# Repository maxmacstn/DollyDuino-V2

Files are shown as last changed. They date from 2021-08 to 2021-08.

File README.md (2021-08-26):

# DollyDuino 2.0
ESP32 Based camera motion controller, implement based on Arduino and PlatformIO. This project is the successor from my [orginal design](https://github.com/maxmacstn/Arduino-Motorized-Dolly).

**Video:**  https://youtu.be/K7UvhgVBU1E

⚠️ This project is currently in the development process, it might contain some unfinished features or bugs. However, it was functioning quite well so far.

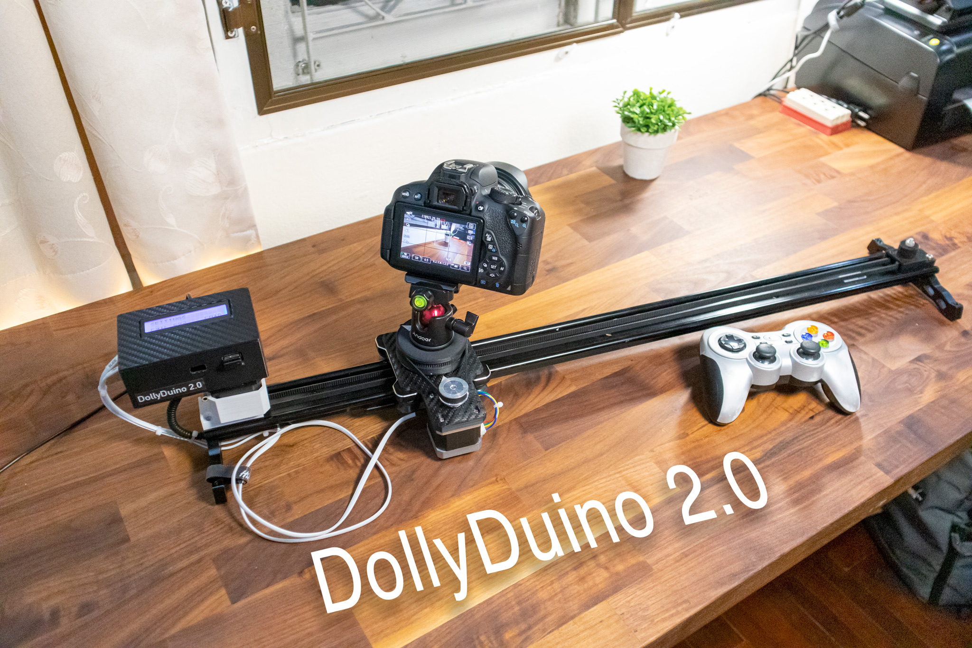
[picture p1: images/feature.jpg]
Bluetooth Remote for Modern Canon Cameras


## Features

* 2 Axis control: Slide & Pan.
* 16x2 LCD Display.
* Controlled by USB HID interface gamepad.
* Built-in Canon EOS Camera remote using Bluetooth LE.
* USB-C PD Power input.
* USB-A power out for powering the camera or charging.

## Modes

1. Manual/Slide - Operate the camera movement manually using a gamepad, or set the automatic linear movement with smooth acceleration/deceleration.
2. Orbit Mode - Lock the camera facing towards the object while sliding.
3. Time lapse - Precise micro-movement with automatic camera triggering system.

## Major components
Please see full list of components and parts in [Bill of Materials](https://github.com/maxmacstn/DollyDuino-V2/blob/main/BOM.xlsx).
- Andeor camera slider.
- DollyDuino 2.0 controller.
	- Node32 Lite development board.
	- TMC2226 silent stepper driver.
	- LCD 16x2 Display.
	- ZY12PDN USB-C PD Module.
	- Mini USB Host shield.
- NEMA 17 Stepper Driver
- GT2 Timing belt and pulley wheels.
- A bunch of 3D-Printed parts.

## Gamepad buttons

| Button | Function |
|---|---|
| A | Trigger camera shutter |
| B | Clear in/out point, Stop auto slide |
| X | Unlock motors |
| Y | Set in/out point |
| Left | Previous mode |
| Right  | Next Mode |
| Up | Increment Interval |
| Down | Decrement Interval |
| LT | Decrement shutter speed |
| RT | Increment shutter speed |
| LB | Decrease sliding speed |
| RB | Increase sliding speed |
| Start  | Start auto sliding movement |
| Back | Override all axis position as home position (0) |

## References 
-  [3D Printed Motorised DSLR Camera Slider by issac879](https://www.youtube.com/watch?v=v1b7Wvu87-U)
- [Mini USB Host shield with esp8266](https://create.arduino.cc/projecthub/139994/plug-any-usb-device-on-an-esp8266-e0ca8a)

## To-do
- [ ] Fix bug in timelapse mode, the slider should not move when the camera shutter is opening.
- [ ] Re-design pan axis to be more rigid.
- [ ] Improve usability.

Feel free to contribute!

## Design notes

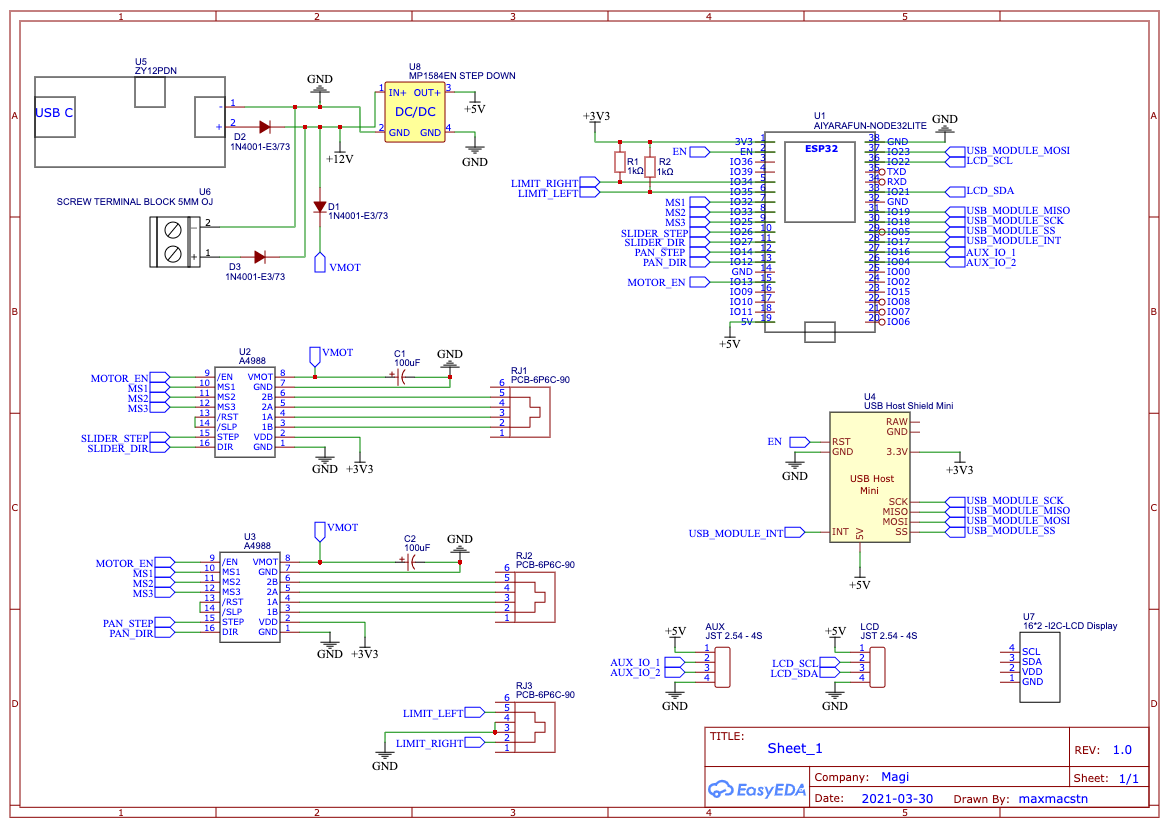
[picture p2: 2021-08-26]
PCB/Schematic_DollyDuino2_2021-08-26.png

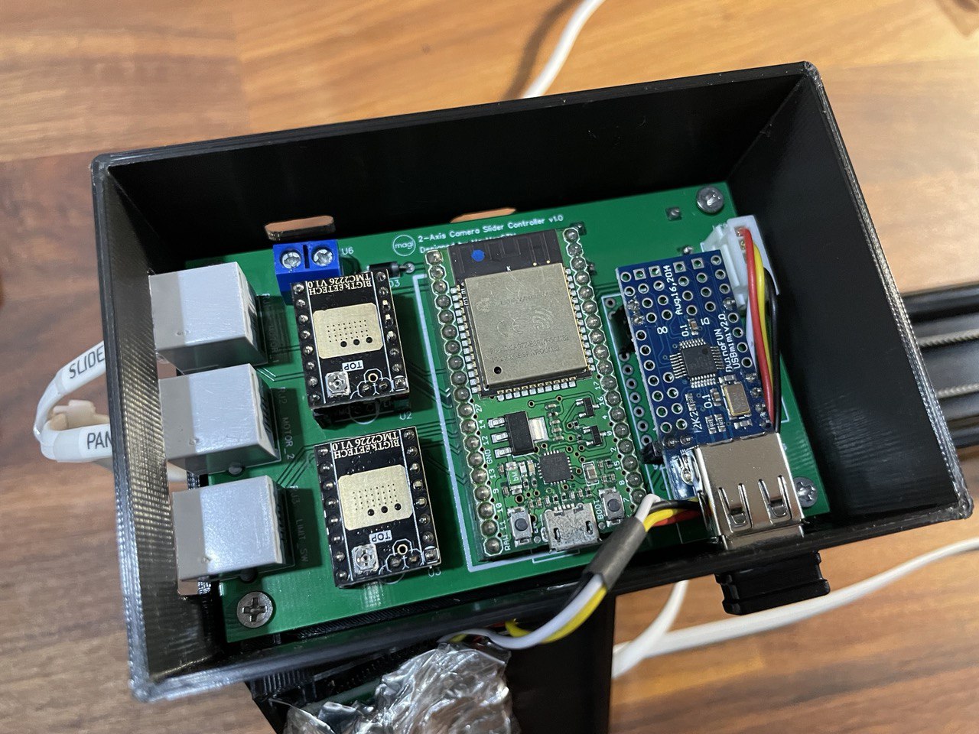
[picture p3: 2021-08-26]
images/controller_inside.jpeg

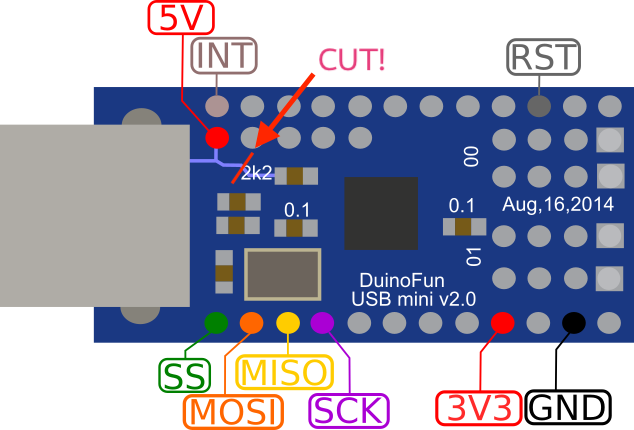
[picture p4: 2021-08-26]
References/usbhost_mini_3v_convert.png

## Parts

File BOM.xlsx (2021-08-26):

DollyDuino2.0 Bill of materials |  |  |  | By MaxMacSTN
Part | Name | Links | Qty
Base | Andoer Slider 80 CM | https://www.lazada.co.th/products/andoer-80-5-ca-nonni-konso-nydslrdv-i302700572-s521866836.html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 | 1
 | Andoer Ball Head small | https://www.lazada.co.th/products/andoer-canon-nikon-sony-dslr-mirrorless-i300828203-s518186201.html?mp=1 | 1
Rail ASSY | GT2 timing belt width 6mm (2 Metres) | https://www.zonemaker.com/product/36/2gt-6mm-rubber-open-timing-belt-%E0%B8%A3%E0%B8%B2%E0%B8%84%E0%B8%B2-1%E0%B9%80%E0%B8%A1%E0%B8%95%E0%B8%A3-2 | 1
 | 2GT Width 6mm, 20 Teeth Timing Pulley (Bore 5mm) | https://www.zonemaker.com/product/65/2gt-width-6mm-20-teeth-timing-pulley-bore-5mm | 1
 | Pulley Wheel 20 Teeth 2GT | https://www.zonemaker.com/product/609/pulley-wheel-20-%E0%B8%9F%E0%B8%B1%E0%B8%99-2gt-width-6mm-belt-bore-5mm | 1
 | Belt closed loop rubber 280-2GT-6 (Closed-loop length 280mm, GT2 timing belt, width 6mm) | https://www.zonemaker.com/product/609/pulley-wheel-20-%E0%B8%9F%E0%B8%B1%E0%B8%99-2gt-width-6mm-belt-bore-5mm | 1
 | [3D Print] slide motor mount |  | 1
 | [3D Print] slide pully wheel mount |  | 1
 | M4 Nuts & Bolts for securing pulley wheel |  | 1
Sliding plate ASSY | 2GT Width 6mm, 36 Teeth Timing Pulley Bore (Bore 5mm) | https://www.zonemaker.com/product/2366/2gt-width-6mm-36-teeth-timing-pulley-bore-bore-5mm | 1
 | GT2 Belt closed loop rubber 280-2GT-6 (Closed-loop length 280mm, GT2 timing belt, width 6mm) | https://www.zonemaker.com/product/1621/belt-closed-loop-rubber-280-2gt-6-closed-loop-length-280mm-gt2-timing-belt-width-6mm-2 | 1
 | Timing Belt Fixing Clamp 9*40mm | https://www.zonemaker.com/product/402/timing-belt-fixing-clamp-9x40mm-tooth-pitch-2mm-aluminum-alloy | 1
 | [3D Print] Timing Belt Clamp mount |  | 1
 | [3D Print] Ball Head Mount Top |  | 1
 | [3D Print] Ball Head Mount Bottom |  | 1
 | [3D Print] Inner Bearing Holder |  | 1
 | [3D Print] Inner Bearing Washer |  | 1
 | [3D Print] Sliding Plate Mount |  | 1
 | [3D Print] Sliding Plate Mount Clamp |  | 1
 | M2x4 Countersunk Screw |  | 1
 | M3x8 Countersunk Screw |  | 1
 | M3x10 Countersunk Screw |  | 1
 | M3x8 Screw |  | 1
 | M6 Bolt |  | 1
 | M3 Nut and Bolt (for belt clamp) |  | 1
 | Deep Grove Bering 6808ZZ (bore:40mm OD:52mm Width:7mm) | https://shopee.co.th/6806ZZ-~-6810ZZ-%E0%B8%95%E0%B8%A5%E0%B8%B1%E0%B8%9A%E0%B8%A5%E0%B8%B9%E0%B8%81%E0%B8%9B%E0%B8%B7%E0%B8%99%E0%B9%80%E0%B8%A1%E0%B9%87%E0%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 | 1
Controller | ESP32 AIYARAFUN-Node32 Lite |  | 1
 | DollyDuino2.0 PCB |  | 1
 | Capacitor 100uF |  | 2
 | Diode 1N4001 |  | 4
 | Resistor 1KΩ 5W |  | 2
 | USB Host Shield Mini |  | 1
 | ZY12PDN USB-C PD Module |  | 1
 | MP1584EN STEP DOWN module 5V |  | 1
 | BIQU TMC2226 V1.0 Stepper Driver | https://shopee.co.th/BIQU-TMC2226-V1.0-Driver-for-3D-Printer-i.43378426.4744022662 | 2
 | JST Header JST 2.54 - 4S |  | 2
 | SCREW TERMINAL BLOCK 5MM |  | 1
 | RJ11 6P6C Female PCB Mount |  | 3
 | LCD 16x2 I2C |  | 1
 | [3D Print] controller_lid |  | 1
 | [3D Print] controller_enclosure_body |  | 1
 | [3D Print] controller_enclosure_lid |  | 1
Motors and wires | Nema 17 Stepper Driver |  | 2
 | Telephone Wire RJ11 4P |  | 1
Gamepad | Logitech F710 |  | 1

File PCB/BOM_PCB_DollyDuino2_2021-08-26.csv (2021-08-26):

ID | Name | Designator | Footprint | Quantity | Manufacturer Part | Manufacturer | Supplier | Supplier Part | Price | Pins | 3DModel | LCSC Assembly | Paste Type | Contributor | SMT Type | link
1 | MP1584EN STEP DOWN | U8 | MP1584EN | 1 |  |  |  |  |  | 4 |  |  |  | zdravko.kreze
2 | 1N4001-E3/73 | D3,D1,D2 | DO-41_BD2.4-L4.7-P8.70-D0.9-RD | 3 | 1N4001-E3/73 | VISHAY | LCSC | C145491 | 0.155 | 2 | DO-41_D2.8-L4.2-P8.00 | Yes | expand | LCSC | Extend | https://item.szlcsc.com/85412.html
3 | A4988 | U2,U3 | A4988 | 2 | A4988 |  |  |  |  | 16 |  |  |  | rom1nux |  | https://www.pololu.com/file/0J450/a4988_DMOS_microstepping_driver_with_translator.pdf
4 | USB Host Shield Mini | U4 | ARDUINO USB HOST SHIELD MINI - BRETT | 1 |  |  |  |  |  | 25 |  |  |  | SparkFun
5 | AIYARAFUN-NODE32LITE | U1 | NODE32S-PCBLIB | 1 | New SchematicLib |  |  |  |  | 38 |  |  |  | marcos.miasiro
6 | 100uF | C1,C2 | CAP-TH_BD5.0-P2.00-D0.8-FD | 2 | 100uF 25V 5*11 | ValuePro | LCSC | C47873 | 0.012 | 2 | CAP-TH_D5.0×H7.0×P2.0 | Yes | expand | 官方封装库 | Extend | https://item.szlcsc.com/44805.html
7 | PCB-6P6C-90 | RJ1,RJ2,RJ3 | RJ11-TH_PCB-6P6C-90 | 3 | - | Shenzhen Cankemeng | LCSC | C189750 | 0.16 | 6 | RJ11-TH_PCB-6P6C-90 | Yes | expand | LCSC | Extend | https://item.szlcsc.com/203237.html
8 | 1kΩ | R1,R2 | RES-TH_BD2.5-L6.5-P10.50-D0.6 | 2 | CF1/4W-1.8KΩ±5%T52 | Huaxing Mechanical-Elec. | LCSC | C714304 | 0.005 | 2 | RES-TH_D2.3-L6.5-P10.50 |  |  | LCSC |  | https://item.szlcsc.com/204066.html
9 | SCREW TERMINAL BLOCK 5MM OJ | U6 | SCREW TERMINAL BLOCK 5MM | 1 | Screw Terminal Block 5mm |  |  |  |  | 2 |  |  |  | luizwenner
10 | JST 2.54 - 4S | AUX,LCD | CONECTOR JST 2.54 - 4S | 2 |  |  |  |  |  | 4 |  |  |  | aristijuango
11 | ZY12PDN | U5 | ZY12PDN | 1 |  |  |  |  |  | 2 |  |  |  | superpolynomialtime

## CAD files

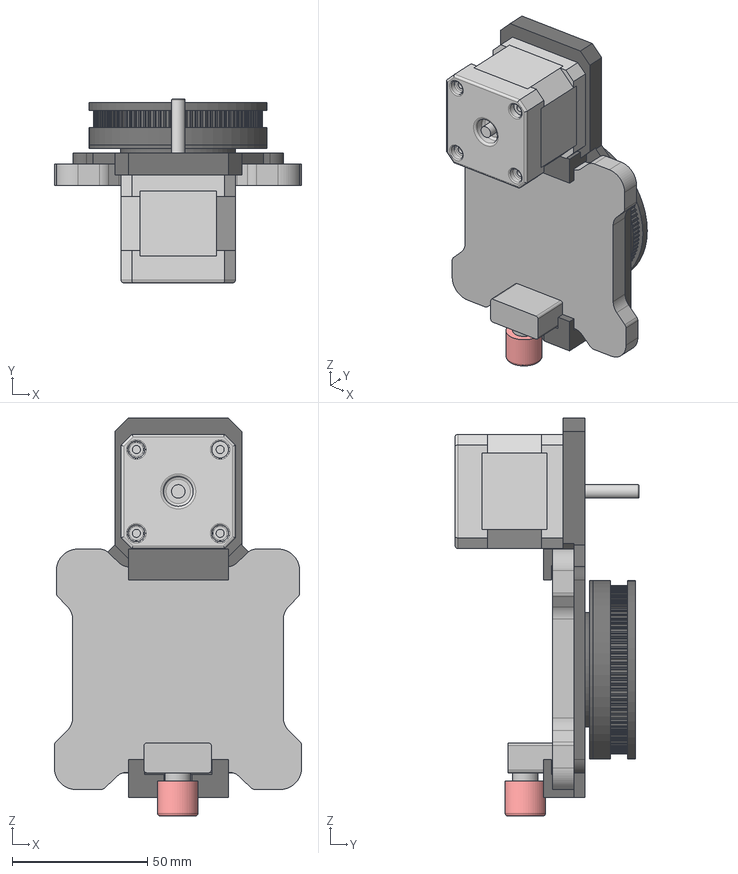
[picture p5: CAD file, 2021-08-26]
3D/STEP/sliding_plate_assy.step
91.5 x 68.0 x 147.3 mm
inner_bearing_holder
inner bearing holder washer
Base
Cuerpo
Tapa
Eje
GT2 Timing Pulley generator v4

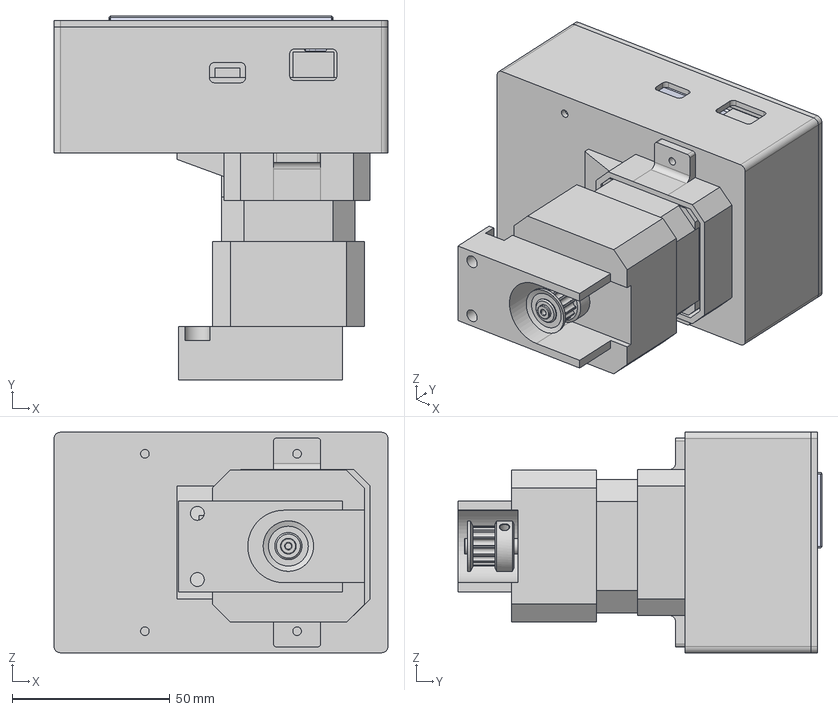
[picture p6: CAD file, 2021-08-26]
3D/STEP/controller_enclosure_assy.step
106.0 x 115.4 x 70.0 mm
PCB
LCD_1
Base
Cuerpo
Tapa
Eje
T5 Pulley

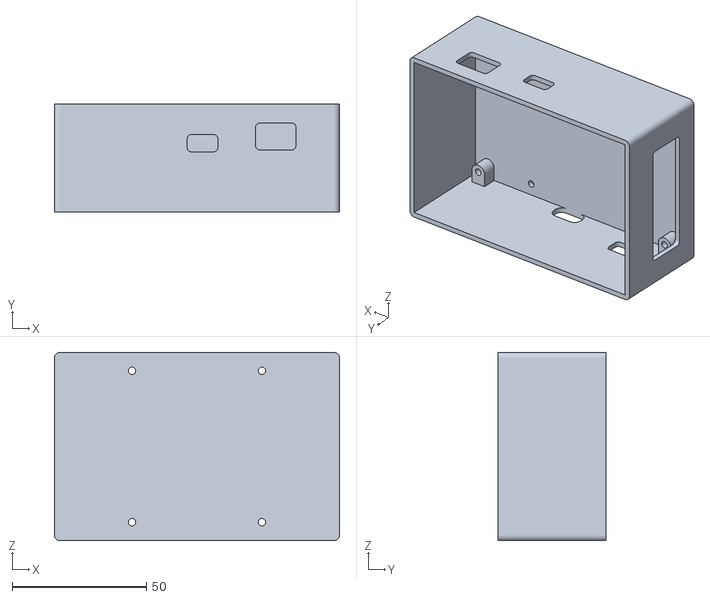
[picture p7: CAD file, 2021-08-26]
3D/STL/controller_enclosure_body.stl
106.0 x 40.0 x 70.0

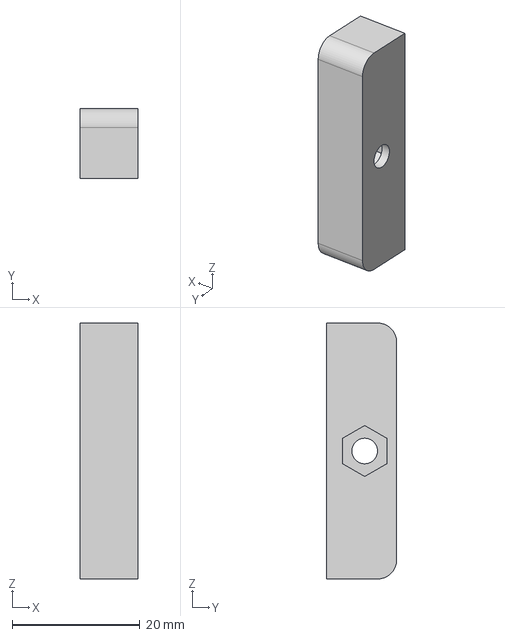
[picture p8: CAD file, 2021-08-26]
3D/STEP/timing_belt_clamp_mount.step
9.00 x 11.0 x 40.0 mm

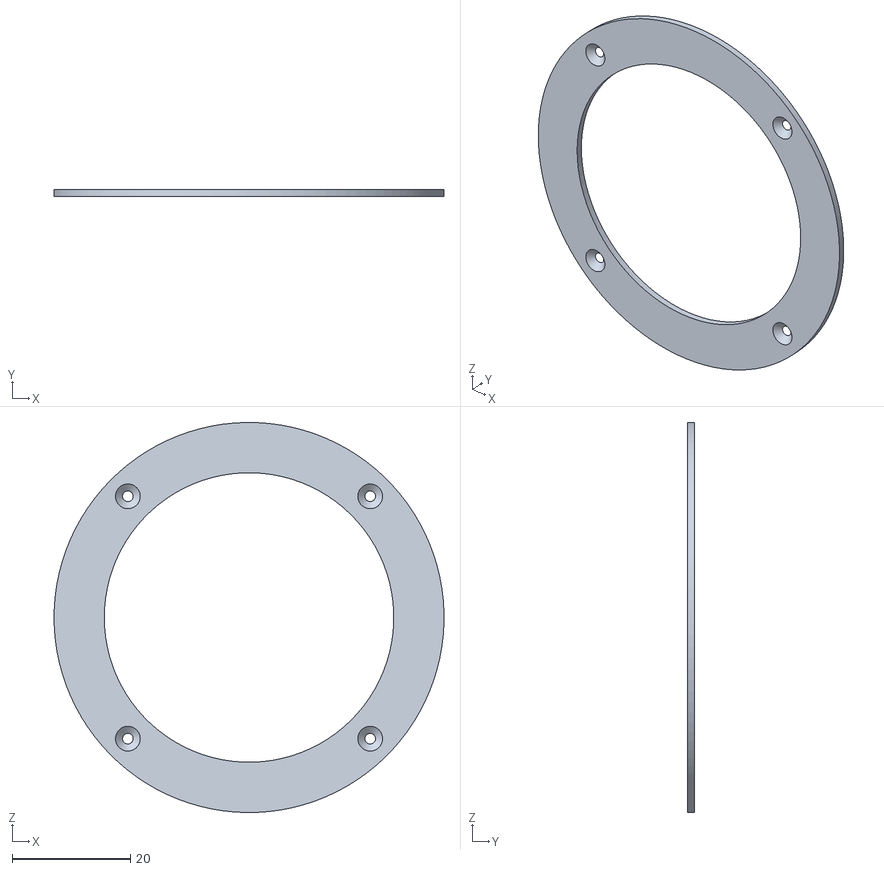
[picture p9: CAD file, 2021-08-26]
3D/STL/ball_head_mount_bottom.stl
66.0 x 1.20 x 66.0

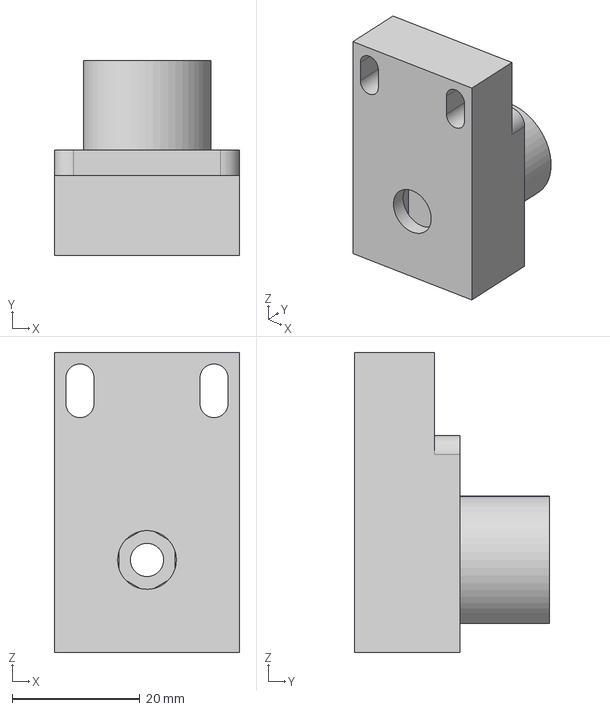
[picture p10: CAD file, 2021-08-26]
3D/STEP/slide_pully_wheel_mount.step
29.0 x 30.5 x 47.0 mm

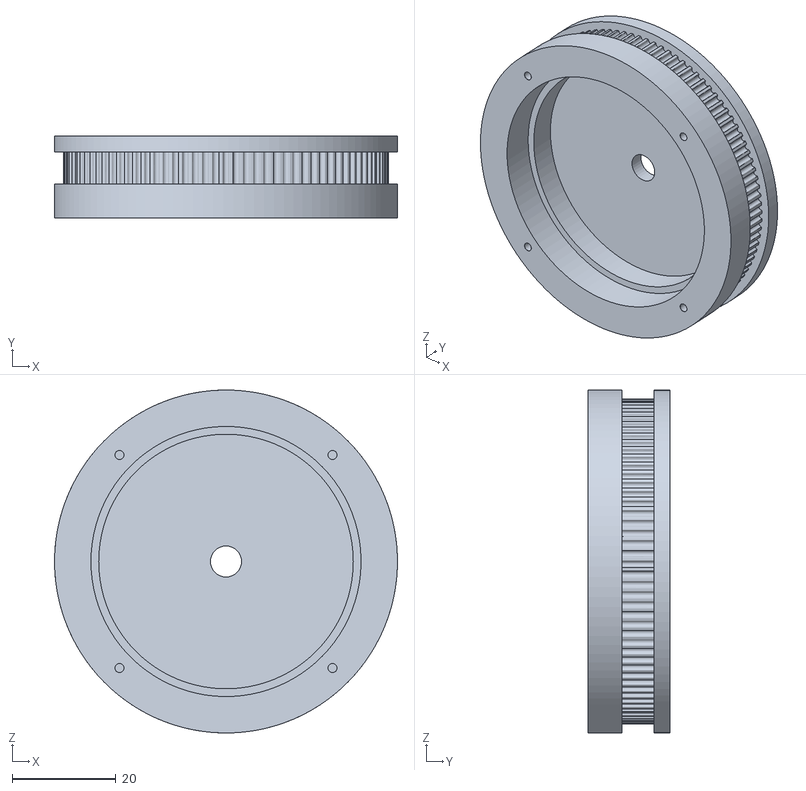
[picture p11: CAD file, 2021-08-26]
3D/STL/ball_head_mount_top.stl
66.0 x 15.7 x 66.0

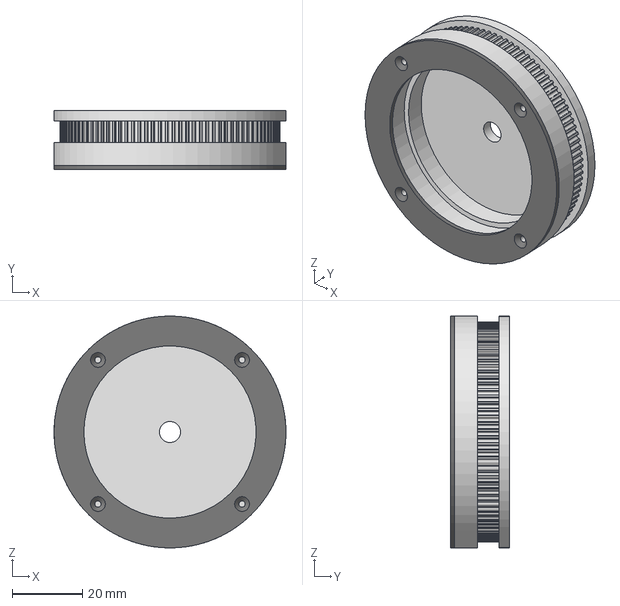
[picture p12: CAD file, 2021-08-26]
3D/STEP/ball_head_mount.step
66.0 x 16.9 x 66.0 mm

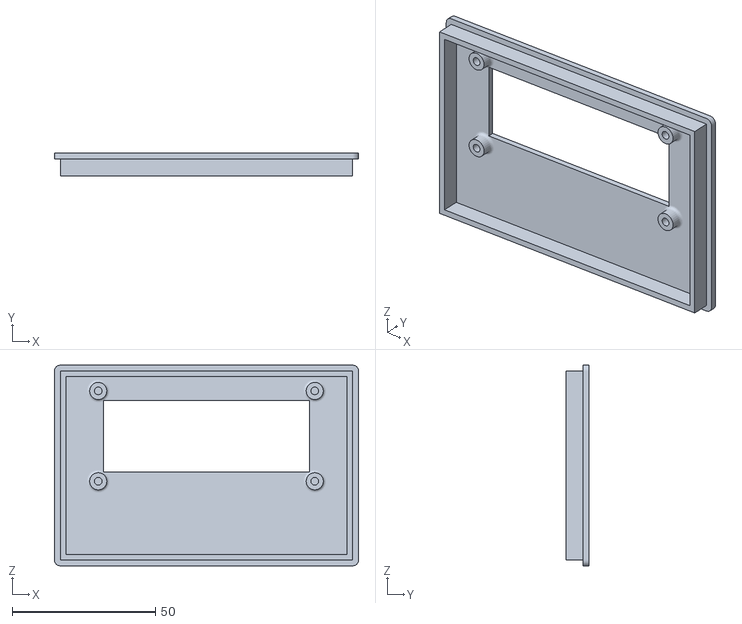
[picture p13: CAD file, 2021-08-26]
3D/STL/controller_lid.stl
106.0 x 8.00 x 70.0

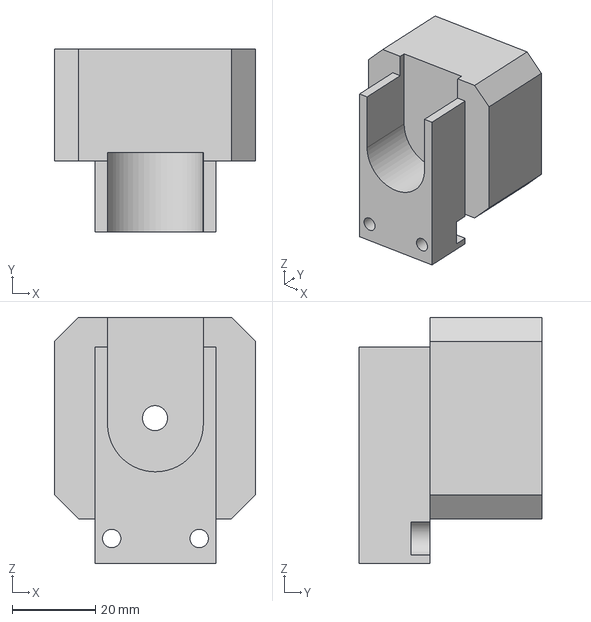
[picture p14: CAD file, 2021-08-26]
3D/STEP/slider_motor_mount.step
48.3 x 43.9 x 59.0 mm

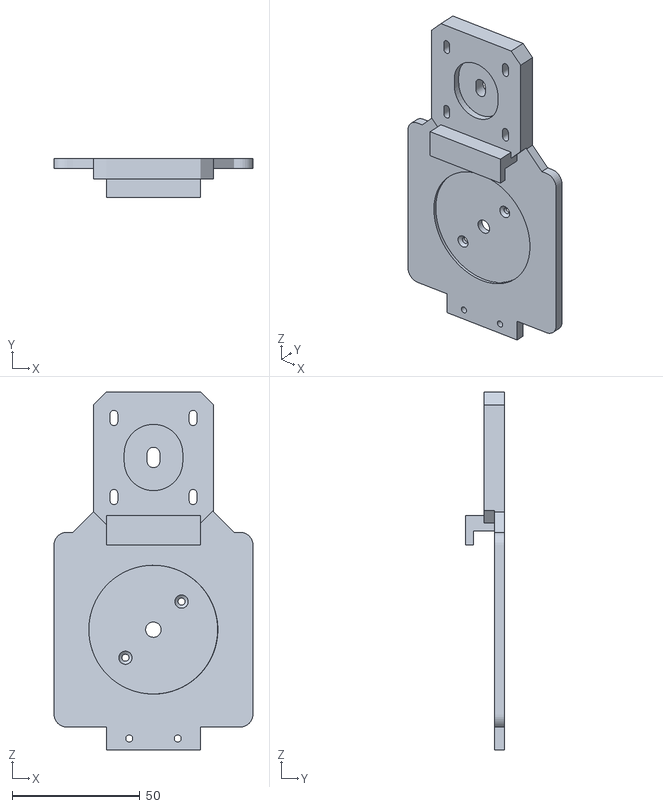
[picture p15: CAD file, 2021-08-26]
3D/STL/sliding_plate_mount.stl
78.0 x 15.3 x 140.3

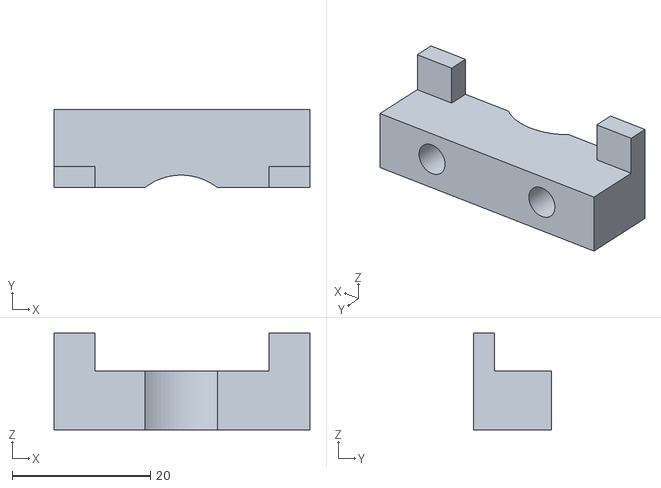
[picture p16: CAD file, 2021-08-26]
3D/STL/sliding_plate_mount_clamp.stl
37.0 x 11.3 x 14.0

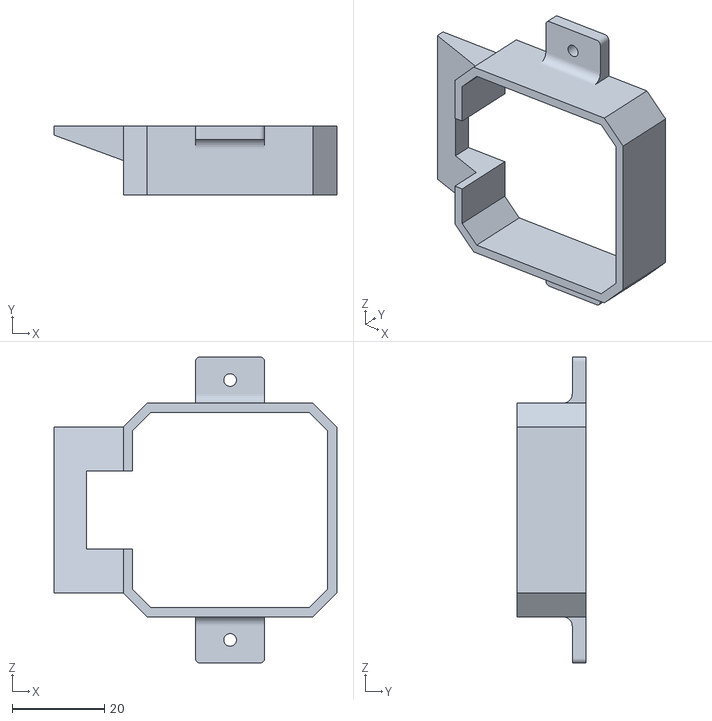
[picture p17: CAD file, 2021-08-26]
3D/STL/controller_enclosure_motor_mount.stl
61.3 x 15.0 x 66.3

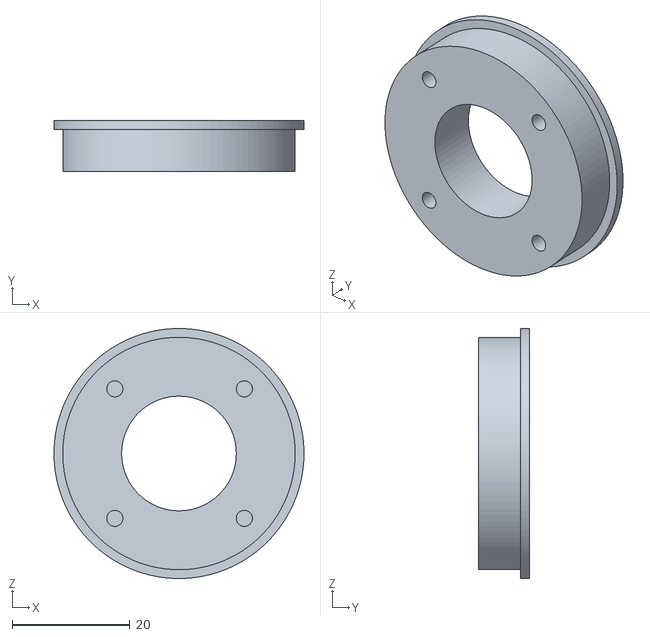
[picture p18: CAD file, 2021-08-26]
3D/STL/inner_bearing_holder.stl
42.5 x 8.60 x 42.5

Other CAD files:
3D/STL/inner_bearing_holder_washer.stl
3D/STL/slide_pully_wheel_mount.stl
3D/STL/slider_motor_mount.stl
3D/STL/timing_belt_clamp_mount.stl

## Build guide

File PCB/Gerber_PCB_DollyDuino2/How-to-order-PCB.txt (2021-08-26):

How to Order PCB

Please refer to:
https://docs.easyeda.com/en/PCB/Order-PCB

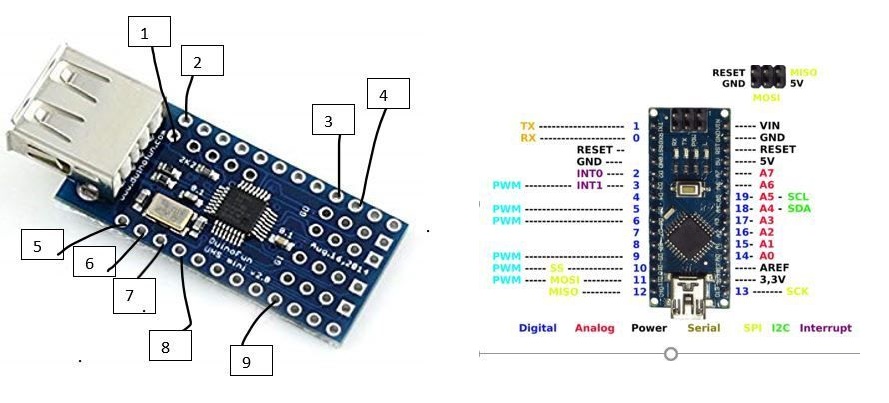
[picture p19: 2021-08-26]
References/arduino_nano_usb_host_shield_wiring_PWkan4VJHw.jpg

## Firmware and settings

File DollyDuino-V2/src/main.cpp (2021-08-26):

#include <Arduino.h>
#include <usbhid.h>
#include <hiduniversal.h>
#include <usbhub.h>
#include "hidjoystickrptparser.h"
#include "Slider.h"
#include "AccelStepper.h"

USB Usb;
USBHub Hub(&Usb);
HIDUniversal Hid(&Usb); //Default pins use P5, P17 for ESP32 board for SPI_SS and INTR
JoystickEvents JoyEvents;
JoystickReportParser Joy(&JoyEvents);
TaskHandle_t usbTaskHandle;

byte gamePadRpos = 127;

Slider slider = Slider();

#define GAMEPAD_BUTTON_A 2
#define GAMEPAD_BUTTON_B 3
#define GAMEPAD_BUTTON_X 1
#define GAMEPAD_BUTTON_Y 4
#define GAMEPAD_BUTTON_UP 00
#define GAMEPAD_BUTTON_DN 04
#define GAMEPAD_BUTTON_L 06
#define GAMEPAD_BUTTON_R 02
#define GAMEPAD_BUTTON_LB 5
#define GAMEPAD_BUTTON_RB 6
#define GAMEPAD_BUTTON_LT 7
#define GAMEPAD_BUTTON_RT 8
#define GAMEPAD_BUTTON_BACK 9
#define GAMEPAD_BUTTON_START 10

void usbTask( void * pvParameters ){
  for(;;){
        Usb.Task();
        vTaskDelay(1);
  }
}



void setup()
{
        // Serial.begin(115200);
        Serial.println("Start");
        slider.init();
        if (Usb.Init() == -1){
                Serial.println("OSC did not start.");
                slider.displayBootMessage("USB Error");
                while(1){};
        }
        delay(200);
        if (!Hid.SetReportParser(0, &Joy)){
                ErrorMessage<uint8_t>(PSTR("SetReportParser"), 1);
                slider.displayBootMessage("USB Parser error");
                while(1){};
        }
        
        slider.displayBootMessage("USB OK!");
        for(int i = 0; i <100; i++){
                Usb.Task();
                delay(10);
        }

        slider.onAnalogStickChanged(0x80, 0x80,  0x80, 0x80);
        
        
}


void loop()
{
        // put your main code here, to run repeatedly:
        Usb.Task();
        slider.run();
        slider.updateScreen();

        // stepper_pan.run();
        // float currentPanSpeed = map(abs(gamePadRpos-128),0,128,0,panDegreesToSteps(180));
        // if (gamePadRpos > 129 ){
        //         stepper_pan.moveTo(stepper_pan.currentPosition() + 1);
        //         stepper_pan.setSpeed(currentPanSpeed);
        // }else if( gamePadRpos < 125 ){
        //         stepper_pan.moveTo(stepper_pan.currentPosition() - 1);
        //         stepper_pan.setSpeed(-currentPanSpeed);

        // }



}

void JoystickEvents::OnGamePadChanged(const GamePadEventData *evt)
{
        Serial.print("X1: ");
        PrintHex<uint8_t>(evt->X, 0x80);
        Serial.print("\tY1: ");
        PrintHex<uint8_t>(evt->Y, 0x80);
        Serial.print("\tX2: ");
        PrintHex<uint8_t>(evt->Z1, 0x80);
        Serial.print("\tY2: ");
        PrintHex<uint8_t>(evt->Z2, 0x80);
        Serial.print("\tRz: ");
        PrintHex<uint8_t>(evt->Rz, 0x80);
        Serial.println("");

        // analogLposX = evt->Y;
        // analogLposY = evt->Z1;
        // analogRposX = evt->Z2;
        // analogRposY = evt->Rz;


        slider.onAnalogStickChanged(evt->Y, evt->Z1,  evt->Z2, evt->Rz);
}

void JoystickEvents::OnHatSwitch(uint8_t hat)
{
        Serial.print("Hat Switch: ");
        PrintHex<uint8_t>(hat, 0x80);
        Serial.println("");

        switch (hat)
        {
        case GAMEPAD_BUTTON_L:
                slider.onPreviousModeButtonPressed();
                break;
        case GAMEPAD_BUTTON_R:
                slider.onNextModeButtonPressed();
                break;
        case GAMEPAD_BUTTON_UP:
                slider.onUpButtonPressed();
                break;
        case GAMEPAD_BUTTON_DN:
                slider.onDnButtonPressed();
                break;
        default:
                break;
        }
}

void JoystickEvents::OnButtonUp(uint8_t but_id)
{
        Serial.print("Up: ");
        Serial.println(but_id, DEC);
        switch (but_id)
        {
        case GAMEPAD_BUTTON_Y:
                slider.disableAllMotors(false);
        

        default:
                break;
        }
}

void JoystickEvents::OnButtonDn(uint8_t but_id)
{
        Serial.print("Dn: ");
        Serial.println(but_id, DEC);

        switch (but_id)
        {
        case GAMEPAD_BUTTON_A:
                slider.onActionButtonPressed();
                // Serial.println("Trigger");
                // canon_ble.triggerPhoto();
                break;
        case GAMEPAD_BUTTON_START:
                slider.onStartButtonPressed();
                break;
        case GAMEPAD_BUTTON_B:
                slider.onBackButtonPressed();
                break;
        case GAMEPAD_BUTTON_LB:
                slider.onLBButtonPressed();
                break;
        case GAMEPAD_BUTTON_RB:
                slider.onRBButtonPressed();
                break;
        case GAMEPAD_BUTTON_Y:
                slider.onAddKeyFrameButtonPressed();
                break;
        case GAMEPAD_BUTTON_LT:
                slider.onLTButtonPressed();
                break;
        case GAMEPAD_BUTTON_RT:
                slider.onRTButtonPressed();
                break;

        case GAMEPAD_BUTTON_X:
                slider.disableAllMotors(true);
                break;
        case GAMEPAD_BUTTON_BACK:
                slider.onSetHomeButtonPressed();
                break;
        
        default:
                break;
        }
}

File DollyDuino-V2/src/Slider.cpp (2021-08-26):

#include "Slider.h"
#include "utils.h"

void Slider::init()
{
    lcd.init(); // initialize the lcd
    lcd.backlight();
    lcd.setCursor(0, 0);
    lcd.print(" DollyDuino 2.0 ");
    delay(100);
    Serial.println("Start init slider");
    lcd.createChar(0, bluetoothChar);
    pinMode({PIN_SLIDE_STEP}, OUTPUT);
    pinMode(PIN_SLIDE_DIR, OUTPUT);
    pinMode(PIN_PAN_STEP, OUTPUT);
    pinMode(PIN_PAN_DIR, OUTPUT);
    pinMode(PIN_SLIDER_LIMIT_LEFT, INPUT_PULLUP);
    pinMode(PIN_SLIDER_LIMIT_RIGHT, INPUT_PULLUP);

    //Setup stepper
    initStepper();
    multiStepper.addStepper(stepper_slide);
    multiStepper.addStepper(stepper_pan);

    //setup AUX pin
    pinMode(PIN_AUX_IO_1, OUTPUT);
    digitalWrite(PIN_AUX_IO_1, LOW);

    //init canon BLE remote lib
    canonBLERemote.init();
    

    Serial.println("Init Complete");
    // lcd.clear();
}

void Slider::displayBootMessage(String msg){
    lcd.setCursor(0,1);
    lcd.print("                ");
    if (msg.length() < 16){
        lcd.setCursor(7 - (msg.length()/2), 1 );
        lcd.print(msg);
    }
}

void Slider::initStepper()
{

    long currentSlidePos = 0;
    long currentPanPos = -panDegreesToSteps(90);

    if (stepper_slide.currentPosition())
    {
        currentSlidePos = stepper_slide.currentPosition();
    }
    if (stepper_pan.currentPosition())
    {
        currentPanPos = stepper_pan.currentPosition();
    }

    pinMode(PIN_MS1, OUTPUT);
    pinMode(PIN_MS2, OUTPUT);
    pinMode(PIN_MS3, OUTPUT);
    pinMode(PIN_MOTOR_EN, OUTPUT);
    digitalWrite(PIN_MS1, HIGH);
    digitalWrite(PIN_MS2, HIGH);
    digitalWrite(PIN_MS3, HIGH);
    digitalWrite(PIN_MOTOR_EN, LOW);
    stepper_pan = AccelStepper(1, PIN_PAN_STEP, PIN_PAN_DIR);
    stepper_slide = AccelStepper(1, PIN_SLIDE_STEP, PIN_SLIDE_DIR);
    stepper_pan.setPinsInverted(INVERT_PAN, false, false);
    stepper_slide.setPinsInverted(INVERT_SLIDE, false, false);
    stepper_pan.setMaxSpeed(panDegreesToSteps(panSpeed));
    stepper_slide.setMaxSpeed(sliderMillimetresToSteps(slideSpeed));
    stepper_slide.setAcceleration(sliderMillimetresToSteps(100));
    stepper_pan.setAcceleration(panDegreesToSteps(360) * 2);

    stepper_slide.setCurrentPosition(currentSlidePos);
    stepper_pan.setCurrentPosition(currentPanPos);
}



void Slider::pairEOSCamera(){

    if (eosPairingProcess == 0){
        Serial.println("Pair EOS Camera");
        eosPairingProcess = 1;
        updateScreen(1);
            bool res = false;
            for (int i = 0; i < 5; i++){
                res =  canonBLERemote.pair(5);
                if (res)
                    break;
            }
            if (res){
                Serial.println("Pairing success");
                eosPairingProcess = 2;
            }else{
                Serial.println("Pairing failed");
                eosPairingProcess = 3;
            }
            updateScreen(1);
            delay(1000);
            eosPairingProcess = 0;
            updateScreen(1);

    }
}

void Slider::onAddKeyFrameButtonPressed(){
    Serial.println("onAddKeyFrameButtonPressed");
    switch (currentMode)
    {
   
    case ORBIT:
        addPosition();
        printKeyframeElements();
        break;
    case SLIDE:
        addPosition();
        printKeyframeElements();
        break;
    case TIMELAPSE:
        addPosition();
        printKeyframeElements();
        break;
    default:
        break;
    }
}

void Slider::onActionButtonPressed()
{
    Serial.println("OnActionButtonPressed");
    switch (currentMode)
    {
   
    case ORBIT:
        triggerCamera();
        break;
    case SLIDE:
        triggerCamera();
        break;
    case TIMELAPSE:
        triggerCamera();
        break;
    case SETTINGS:
        pairEOSCamera();
    default:
        break;
    }
}

void Slider::onLBButtonPressed()
{

    if (currentMode == TIMELAPSE)
    {
        if (timelapseSelectedtime > 0)
        {
            timelapseSelectedtime = (timelapseSelectedtime - 1);
        }
    }
    else
    {

        if (currentSpeedScale > 0.1)
        {
            currentSpeedScale -= 0.1;
            slideSpeed = MAX_SLIDE_SPEED * currentSpeedScale;
            panSpeed = MAX_PAN_SPEED * currentSpeedScale;
            stepper_pan.setMaxSpeed(panDegreesToSteps(panSpeed));
            stepper_slide.setMaxSpeed(sliderMillimetresToSteps(slideSpeed));
        }
    }
}

void Slider::onRBButtonPressed()
{

    if (currentMode == TIMELAPSE)
    {
        if (timelapseSelectedtime < 7)
        {
            timelapseSelectedtime = timelapseSelectedtime + 1;
        }
    }
    else
    {
        if (currentSpeedScale < 1)
        {
            currentSpeedScale += 0.1;
            slideSpeed = MAX_SLIDE_SPEED * currentSpeedScale;
            panSpeed = MAX_PAN_SPEED * currentSpeedScale;
            stepper_pan.setMaxSpeed(panDegreesToSteps(panSpeed));
            stepper_slide.setMaxSpeed(sliderMillimetresToSteps(slideSpeed));
        }
    }
}

void Slider::onLTButtonPressed()
{
    if (currentMode == TIMELAPSE)
    {
        if (timelapseShutterTime > 0)
        {
            timelapseShutterTime -- ;
        }
    }

}

void Slider::onRTButtonPressed(){
        if (currentMode == TIMELAPSE)
    {
        if (timelapseShutterTime <30 )
        {
            timelapseShutterTime ++;
        }
    }
}
void Slider::onUpButtonPressed(){
    if(currentMode == TIMELAPSE && timelapseInterval < 9 )
        timelapseInterval ++;
}

void Slider::onDnButtonPressed(){
    if(currentMode == TIMELAPSE && timelapseInterval > 0)
        timelapseInterval --;
}

uint32_t Slider::panDegreeToStep(float angle)
{
    return pan_steps_per_degree * angle;
}

void Slider::onAnalogStickChanged(byte LposX, byte LposY, byte RposX, byte RposY)
{

    // Remove deadzones
    if (abs(LposX - 128) <= ANALOG_DEADZONE)
    {
        LposX = 128;
    }
    if (abs(RposX - 128) <= ANALOG_DEADZONE)
    {
        RposX = 128;
    }

    currentAnalogStick.LposX = LposX;
    currentAnalogStick.LposY = LposY;
    currentAnalogStick.RposX = RposX;
    currentAnalogStick.RposY = RposY;
    // switch (currentMode)
    // {
    // case (MANUAL):

    //     currentAnalogStick.LposX = LposX;
    //     currentAnalogStick.LposY = LposY;
    //     currentAnalogStick.RposX = RposX;
    //     currentAnalogStick.RposY = RposY;

    //     break;
    // case (ORBIT):

    //     currentAnalogStick.LposX = LposX;
    //     currentAnalogStick.LposY = LposY;
    //     currentAnalogStick.RposX = RposX;
    //     currentAnalogStick.RposY = RposY;

    //     break;
    // }
}

float Slider::panDegreesToSteps(float angle)
{
    return pan_steps_per_degree * angle;
}

long Slider::sliderMillimetresToSteps(float mm)
{
    return round(mm * slider_steps_per_millimetre);
}

/*--------------------------------------------------------------------------------------------------------------------------------------------------------*/
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
